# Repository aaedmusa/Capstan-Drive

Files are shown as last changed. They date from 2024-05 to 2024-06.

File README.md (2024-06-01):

# Capstan-Drive
A Capstan Drive is a cheap rope-driven speed reducer that has low backlash, low inertia, low noise, and high torque transparency. 
When it comes to building robots a Capstan Drive can be quite beneficial. This test stand has the following features:

-3D printed in PLA

-Weighs 852g

-120° rotation

-8.55:1 reduction (quasi-direct drive)

-Helical pattern on both drums for guided unraveling

-Lead screw to tension the rope

-ODrive S1 FOC Controller

-Eagle Power 90KV BLDC Motor

Test Stand5

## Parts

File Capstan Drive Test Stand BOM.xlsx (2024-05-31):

Capstan Drive Test Stand BOM
Name of Component | Price | Units Sold | Units Needed | Cost of Needed Units
ODrive S1 (w/Screw Terminals) (https://odriverobotics.com/shop/odrive-s1) | $149.00 | 1 | 1 | $149.00
⌀8 x 2.5mm Encoder Magnet (https://www.andymark.com/products/redline-encoder-magnet) | $1.75 | 1 | 1 | $1.75
Eaglepower 8308 Brushless Motor 90KV (https://www.aliexpress.us/item/2255800377511662.html) | $61.00 | 1 | 1 | $61.00
Dyneema DM20 2mm Rope (https://www.amazon.com/dp/B079C73DQX?psc=1&ref=ppx_yo2ov_dt_b_product_details) | $26.49 | 100 ft | 1 ft | $0.26
40x50x6mm Bearings (https://www.amazon.com/dp/B085NDM5WV?psc=1&ref=ppx_yo2ov_dt_b_product_details) | $8.59 | 1 | 2 | $17.18
3x10x4mm Bearings (https://www.amazon.com/uxcell-Groove-Bearing-Double-Bearings/dp/B07FW389P1?sp_csd=d2lkZ2V0TmFtZT1zcF9hdGY) | $13.79 | 20 | 4 | $2.76
15x28x7mm Bearing (https://www.amazon.com/dp/B07FWC3SJD?psc=1&ref=ppx_yo2ov_dt_b_product_details) | $9.89 | 8 | 1 | $1.24
M3 x 6mm Inserts (https://www.amazon.com/gp/product/B07LBQRYR3/ref=ppx_yo_dt_b_search_asin_title?ie=UTF8&psc=1) | $8.59 | 50 | 7 | $1.20
M3 x 5mm Hex Standoffs (https://www.amazon.com/DTGN-M3x5mm-DXL-Standoff-Electronic/dp/B0BC8X9CPK) | $7.99 | 25 | 4 | $1.28
M3 x 10mm Hex Standoffs (https://www.amazon.com/Straight-Pillar-Female-Threaded-Standoff/dp/B09B1RBLT4) | $14.93 | 100 | 2 | $0.30
M3 Locknuts (https://www.amazon.com/100Pcs-Stainless-Self-Lock-Inserted-Clinching/dp/B075ZZW7VL) | $6.99 | 100 | 2 | $0.14
M3 x 6mm Screws (https://www.amazon.com/Fullerkreg-Socket-Stainless-Machine-Quantity/dp/B07CJ7PDYT) | $7.89 | 100 | 1 | $0.08
M3 x 10mm Countersunk Screws (https://www.amazon.com/dp/B07DWVDDWC?psc=1&ref=ppx_yo2ov_dt_b_product_details) | $6.20 | 100 | 4 | $0.25
M3 x 10mm Screws (https://www.amazon.com/Fullerkreg-Socket-Stainless-Machine-Quantity/dp/B07CK3RSN3) | $7.69 | 100 | 7 | $0.54
M3 x 45mm Screws (https://www.amazon.com/dp/B089KRYJ9Q?psc=1&ref=ppx_yo2ov_dt_b_product_details) | $8.42 | 50 | 4 | $0.67
M3 x 55mm Screws (https://www.amazon.com/dp/B0BGM9N73R?ref=ppx_yo2ov_dt_b_product_details&th=1) | $9.36 | 50 | 2 | $0.37
M4 Locknuts (https://www.amazon.com/gp/product/B08LMNFS5P/ref=ewc_pr_img_1?smid=A7L3QGQ9OUIWY&psc=1) | $5.59 | 50 | 6 | $0.67
M4 x 14mm Screws (https://www.amazon.com/M4x12mm-M4-0-7x12mm-Stainless-Machine-Quantity/dp/B0CLGWZSLT) | $8.89 | 75 | 4 | $0.47
M4 x 25mm Screws (https://www.amazon.com/M4-0-70-Button-Stainless-Fullerkreg-Plastic/dp/B07H17FB12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) | $8.89 | 50 | 2 | $0.36
M4 x 30mm Screws (https://www.amazon.com/M4-0-70-Button-Stainless-Fullerkreg-Plastic/dp/B07H146QMW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) | $8.89 | 25 | 2 | $0.71
M4 x 70mm Screws (https://www.amazon.com/iExcell-Stainless-Socket-Screws-Wrench/dp/B089NC5SCF?s=industrial) | $8.36 | 25 | 4 | $1.34
Total Cost |  |  |  | $241.57

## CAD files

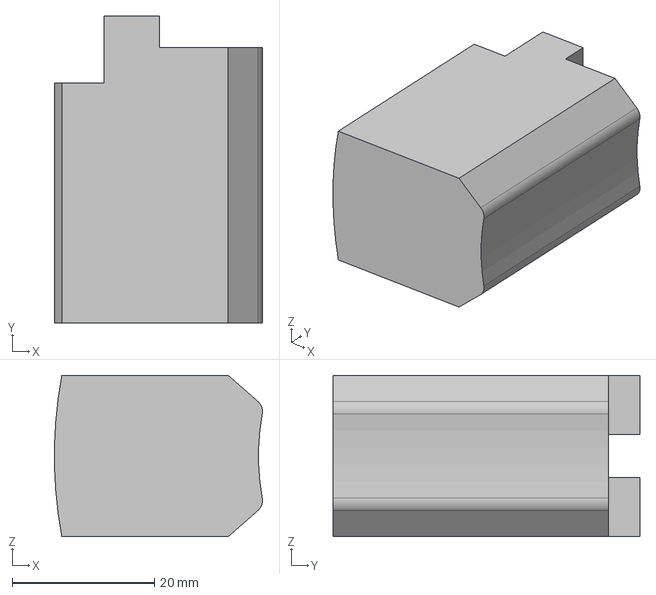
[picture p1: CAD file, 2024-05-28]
STEP Files/Assembly_Jig.stp
29.2 x 43.1 x 22.7 mm

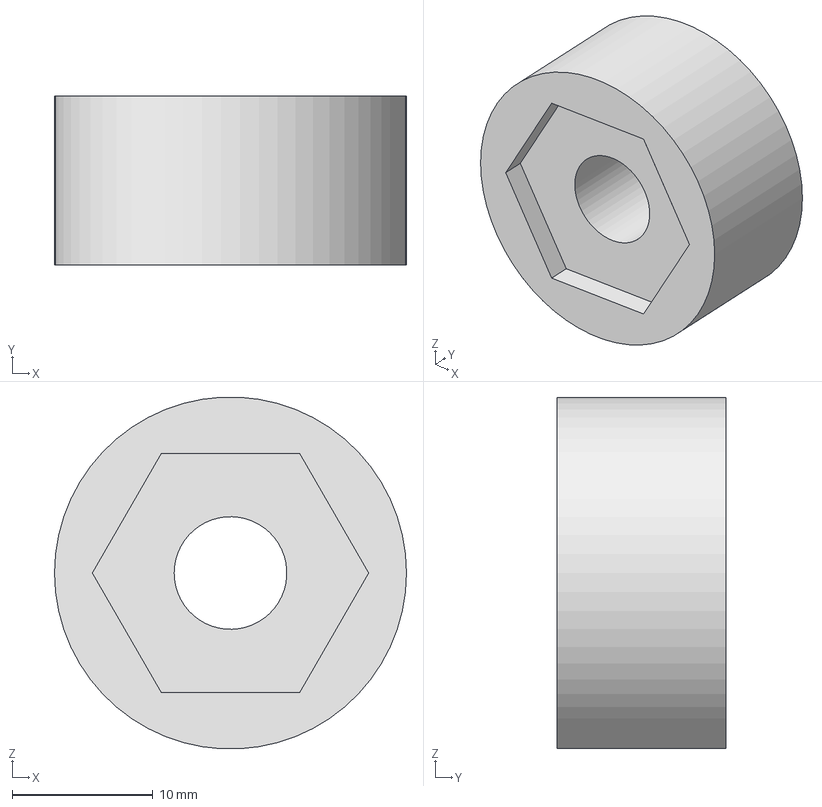
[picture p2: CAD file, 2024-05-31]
STEP Files/Motor_Magnet_Holder.stp
25.0 x 12.0 x 25.0 mm

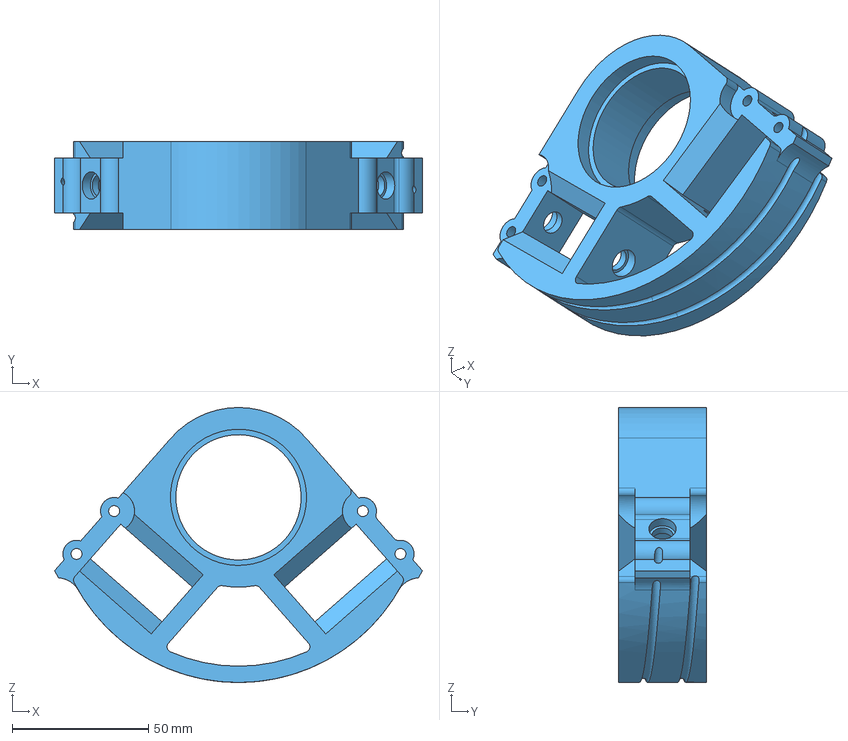
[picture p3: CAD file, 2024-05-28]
STEP Files/Big_Drum.stp
135.1 x 32.2 x 101.0 mm

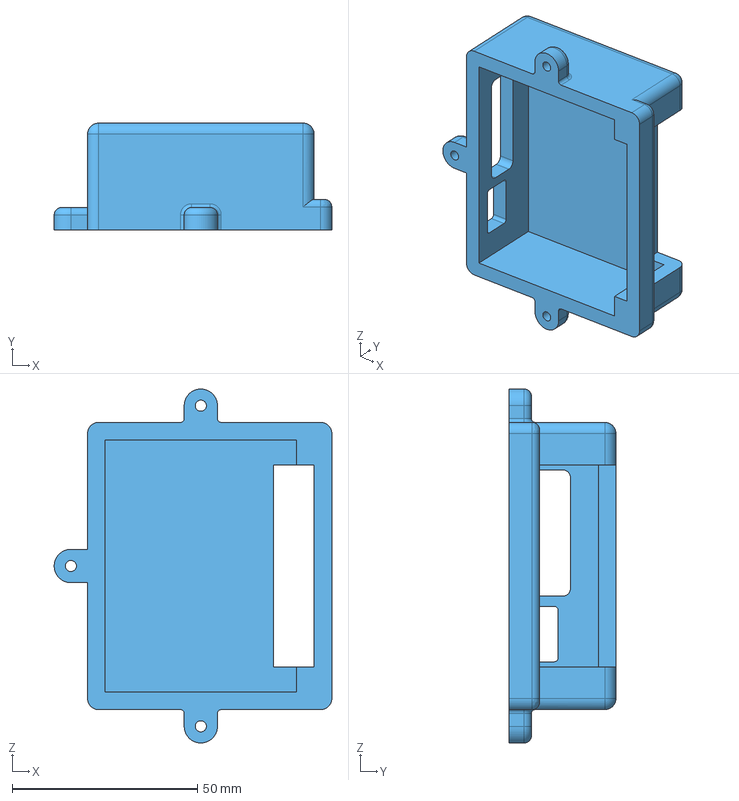
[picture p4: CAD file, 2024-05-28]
STEP Files/ODrive_S1_Single_Cover.stp
74.9 x 28.8 x 95.5 mm

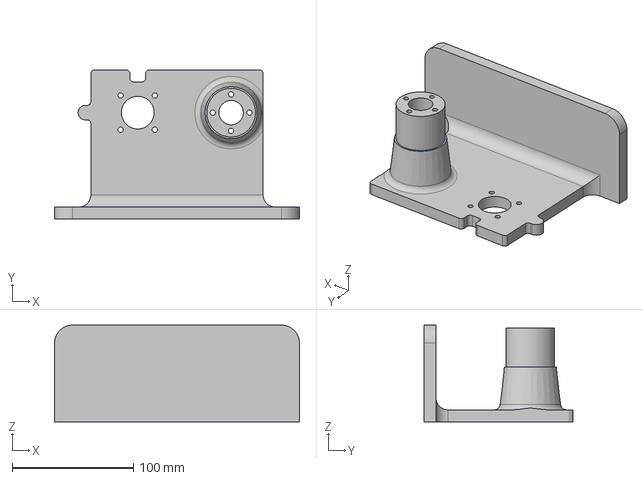
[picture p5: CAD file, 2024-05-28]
STEP Files/Base_Plate.stp
202.4 x 123.3 x 80.0 mm

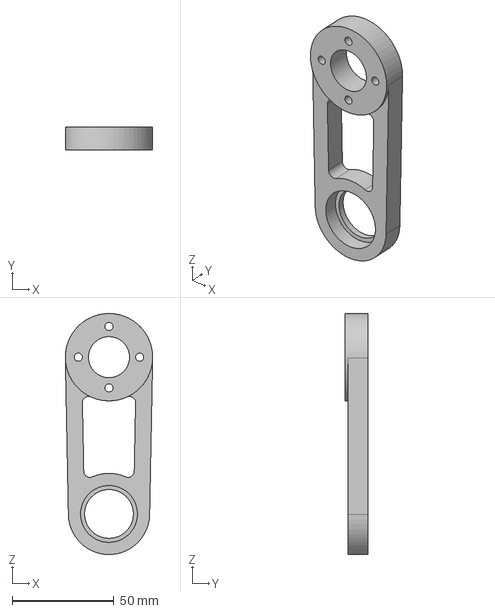
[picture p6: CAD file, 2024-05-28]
STEP Files/Brace.stp
43.0 x 11.5 x 118.6 mm

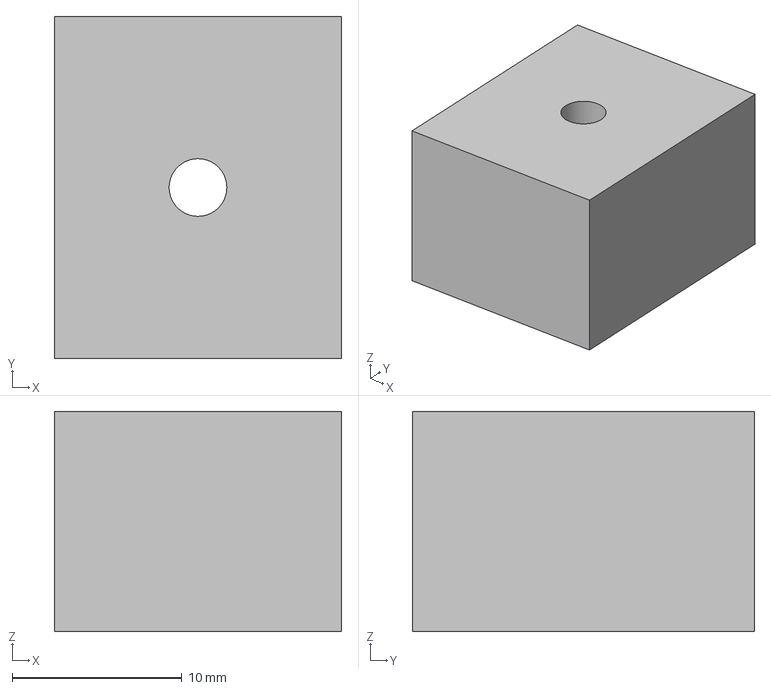
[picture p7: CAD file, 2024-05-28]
STEP Files/Slider.stp
16.9 x 20.2 x 13.0 mm

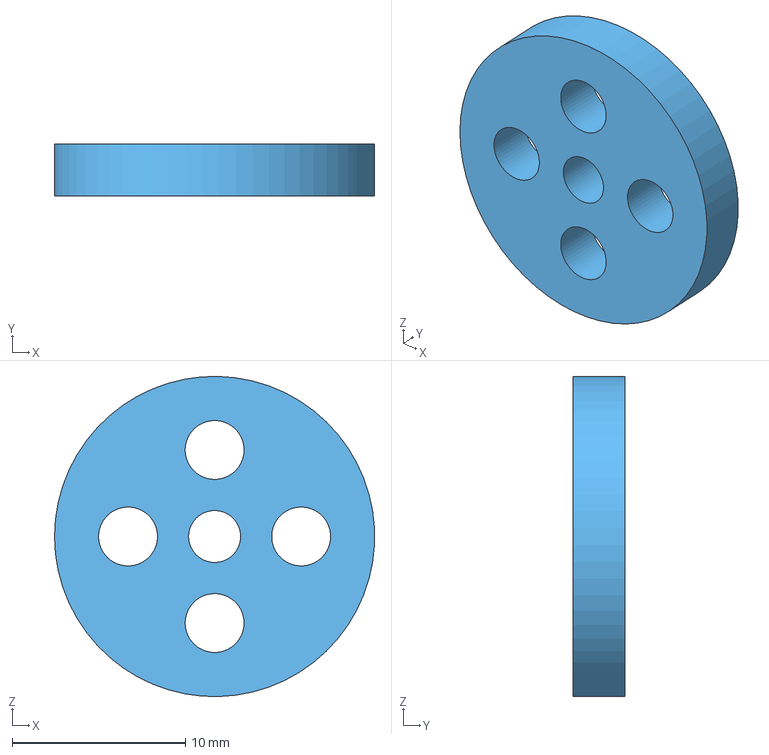
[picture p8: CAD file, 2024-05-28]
STEP Files/Small_Drum_Cap.stp
18.5 x 3.00 x 18.5 mm

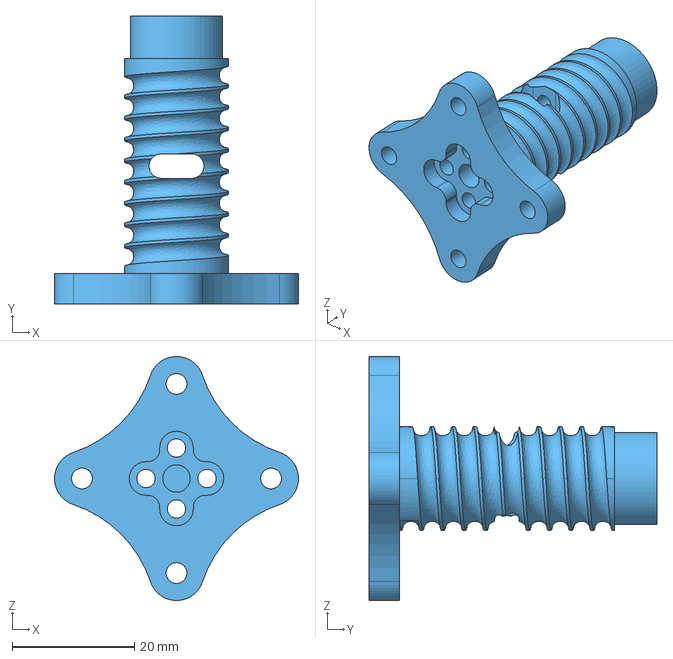
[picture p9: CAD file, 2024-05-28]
STEP Files/Small_Drum.stp
40.0 x 47.2 x 40.0 mm

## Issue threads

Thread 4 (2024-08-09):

Test Code

cguweb-com, 2024-08-09:
love your work, been following you since the servo days.  You inspired me to start working with actuators.

could you share some example code and the hardware you are running, perhaps?  I believe you're using an odrive controller, what about the MCU?
